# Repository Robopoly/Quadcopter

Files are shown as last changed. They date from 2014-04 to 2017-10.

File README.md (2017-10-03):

# Quadcopter shield

## Introduction
This shield has initially been designed by Robopoly for Aeropoly.
It is made for the [PRismino][prismino], and thus compatible with a Leonardo and most Arduino boards.
It is basically a copy of the nanowii board, except that it is now set as a shield for a Leonardo, rather than a standalone board. The pins are exactly the same.
Therefore, you can use the [Multiwii][multiwii] code, but you will have to make your own configuration.
You can find the Altium and gerber files, as well as the datasheets on this repo.

## Components
The shield has an MPU-9250, a barometer and an attiny4313 that is responsible for the GPS, sonar and optic flow sensor.
The MPU-9250 does not have the same register map as the MPU-9150 previously used if I'm not mistaken. Check that before use.

| chip | purpose | link | Status |
|---|---|---|---|
| MPU-9250 | Accelerometer, gyroscope, magnetometer | [MPU-9250][MPU-9250] | Should work |
| TLV70033DDCR | 3V regulator | [TLV70033DDCR][TLV70033DDCR] | Working |
| PCA9306DP1-G | I2C level translator | [PCA9306DP1-G][PCA9306DP1-G] | Working |
| MS5611 | Barometer | [MS5611] [MS5611] | Should work |
| attiny4313 | Handles optical flow sensor and GPS | [attiny4313][attiny4313] | Not tested |
| hc-05 | Bluetooth | NA | Not working |

Check these against the datasheets. I might have messed up.

| identifier | value |
|---|---|
| R1 -> R5 | 10kOhm |
| R6,8,10 | 1kOhm |
| R7,9 | 2kOhm |
| C5,6,8,9,10  | 0.1uF |
| C7,11 |  10nF |

## Power
You can power the controller through the shield by connecting an 5V BEC to ESC1 pin.
The 3.3V available with the micromatch or double pins are not the ones from the Arduino. Meaning you won't fry your controller if you use too much current.
However, you should stick well within the limits as it powers the MPU-9150 and the I2C level shifter.

## Used pins

### ESC connections
Be careful, only ESC 1 has the ground and 5V pins connected. This is made to avoid ground loops.
The data pin is at the outer side of the board (closest to the pins). The ground pin is the square one.

| ESC  | pin |
|---|---|
| ESC1 | 9 |
| ESC2 |  10 |
| ESC3 | 5 |
| ESC4 | 6 |

### Transmitter connections
Be careful, only THR has the ground and 5V pins connected. This is made to avoid ground loops. If your transmitter does not have a common ground for its channels, you will have to bridge the whole ground line, or mod your receiver.
The data pin is at the outer side of the board (closest to the edge). The ground pin is the square one.

| Command | pin  |
|---|---|
| THR | 7  |
| ROLL | MOSI |
| YAW | SCK  |
| PITCH | MISO |
| AUX1 |  8 |

## Thanks
I'd like to thank the various people that have helped developping this board and namely Felix (aka ronco on multiwii forum), the creator of the Nanowii board.

## Previous version

Previous version (V1, as V2 has never been tested) uses only MPU-9150. The MPU-9150 has the same register map as its brother the MPU-6050 which is used in a Nanowii board. Therefore you can use it as a MPU-6050 if you don't want the magnetometer. This might not be valid for MPU-9250.

| identifier | value |
|---|---|
| R1 -> R5 | 10kOhm |
| C1,2,5,6,7 | 0.1uF |
| C4 |  10nF |
| C3 | 2.2nF |

### MPU-9150
Be careful that the axis for the magnetometer are not the same as for the accelerometer and the gyroscope. The ones on the board are those of the accelerometer.

### Jumper
Either J0 or J1 has to be bridged. If you bridge both, you'll short your power. Never bridge both. These are used to set the address of the MPU-9150.

### ESC connections
Be careful, only ESC 1 has the ground and 5V pins connected. This is made to avoid ground loops.
The data pin is at the outer side of the board (closest to the pins). The ground pin is the square one.

| ESC  | pin |
|---|---|
| ESC1 | 9 |
| ESC2 |  10 |
| ESC3 | 5 |
| ESC4 | 6 |

### Transmitter connections
Be careful, only THR has the ground and 5V pins connected. This is made to avoid ground loops. If your transmitter does not have a common ground for its channels, you will have to bridge the whole ground line, or mod your receiver.
The data pin is at the outer side of the board (closest to the edge). The ground pin is the square one.

| Command | pin  |
|---|---|
| THR | 7  |
| ROLL | MOSI |
| YAW | SCK  |
| PITCH | MISO |
| AUX1 |  8 |

[MS5611]: http://www.te.com/commerce/DocumentDelivery/DDEController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 "MS5611"
[MPU-9250]: http://www.invensense.com/mems/gyro/nineaxis.html "MPU-9250"
[MPU-9150]: http://www.invensense.com/mems/gyro/nineaxis.html "MPU-9150"
[TLV70033DDCR]: http://www.ti.com/product/tlv70033 "TLV70033DDCR"
[atmega32u4]: http://www.atmel.ch/Images/doc7766.pdf "ATmega16U4/32U4 datasheet"
[attiny4313]: http://www.atmel.com/images/doc8246.pdf "attiny4313 datasheet"
[PCA9306DP1-G]: http://www.nxp.com/products/interface_and_connectivity/i2c/i2c_voltage_level_translators/PCA9306DP1.html "PCA9306DP1-G"
[prismino]: https://github.com/Robopoly/PRismino "PRismino"
[multiwii]: http://www.multiwii.com/software "Multiwii"

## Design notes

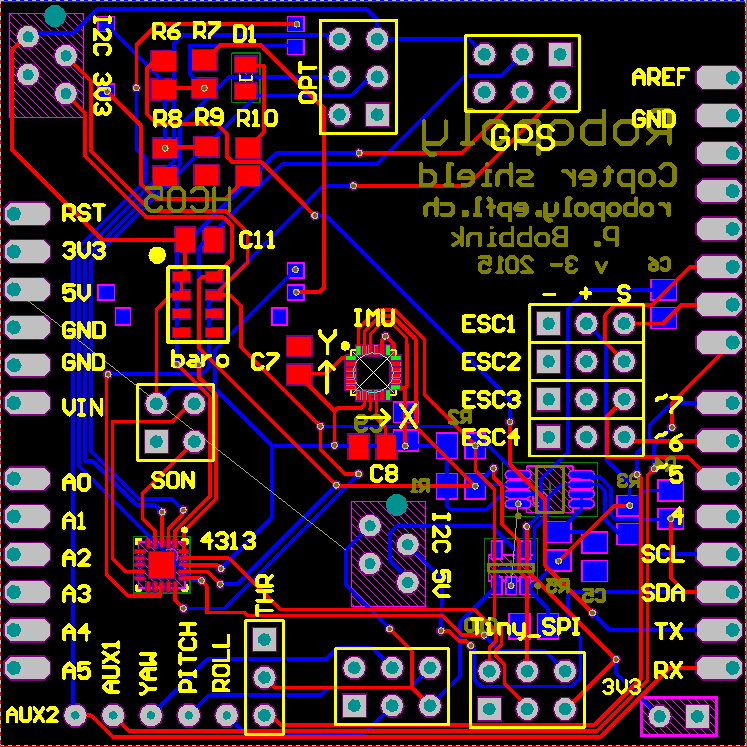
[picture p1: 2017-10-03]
pcb_layout.png

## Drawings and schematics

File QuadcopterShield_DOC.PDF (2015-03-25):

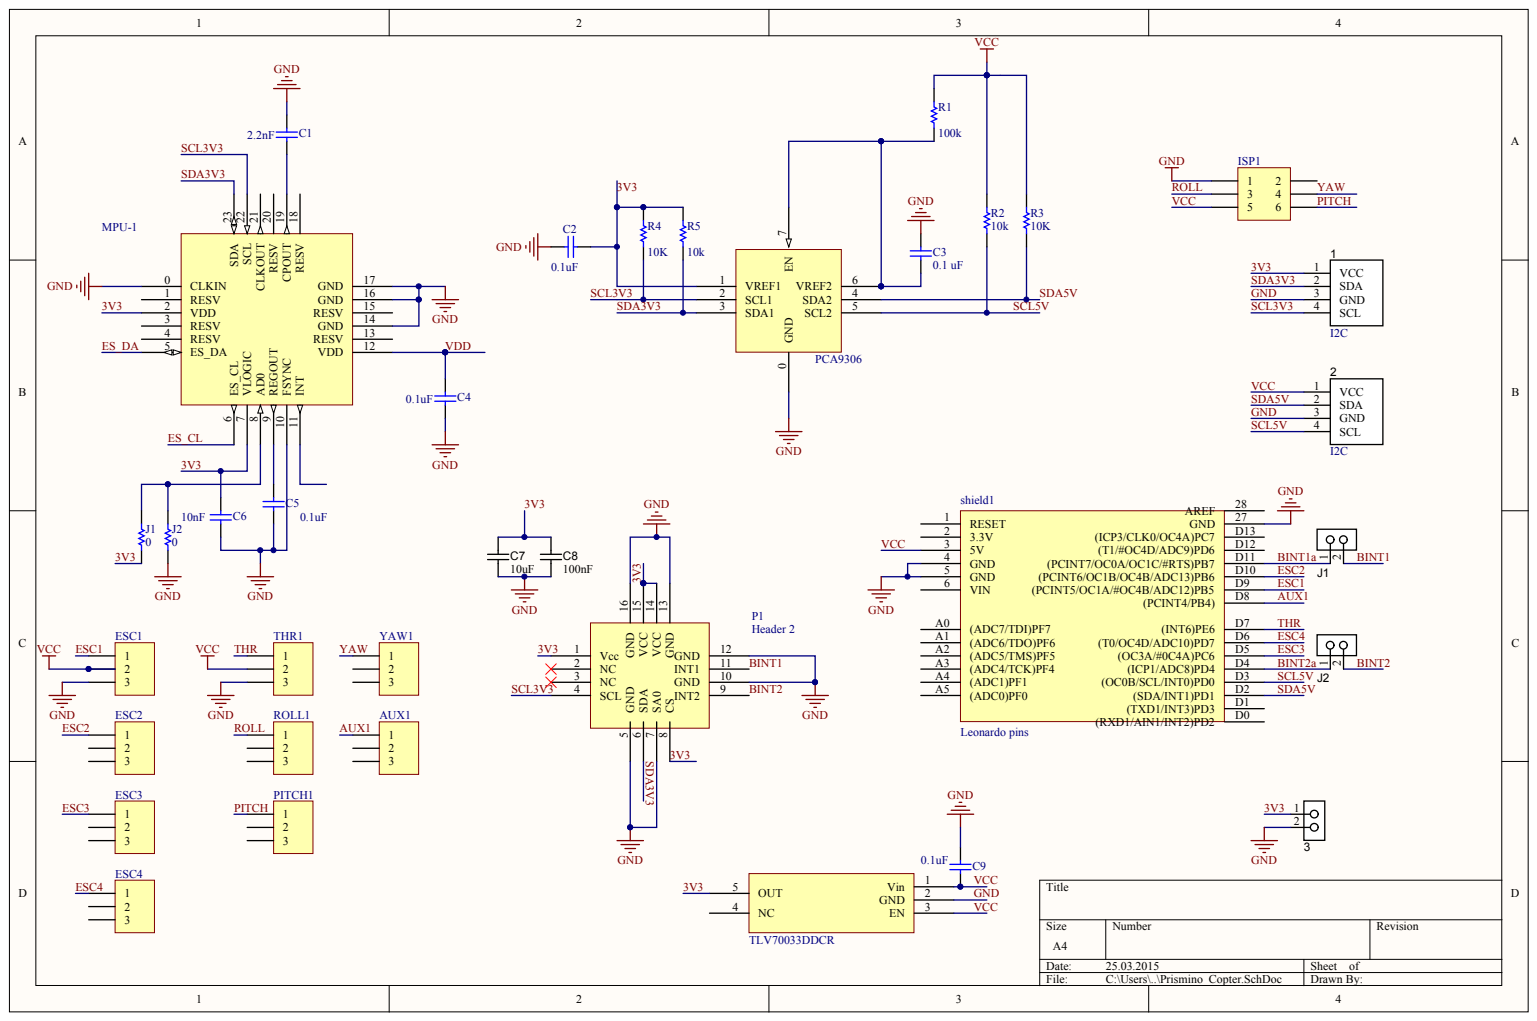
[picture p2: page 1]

RESV 18 CPOUT 19 RESV 20 CLKOUT 21 SCL 22 SDA 23

GND 13 VCC 14 VCC 15 GND 16

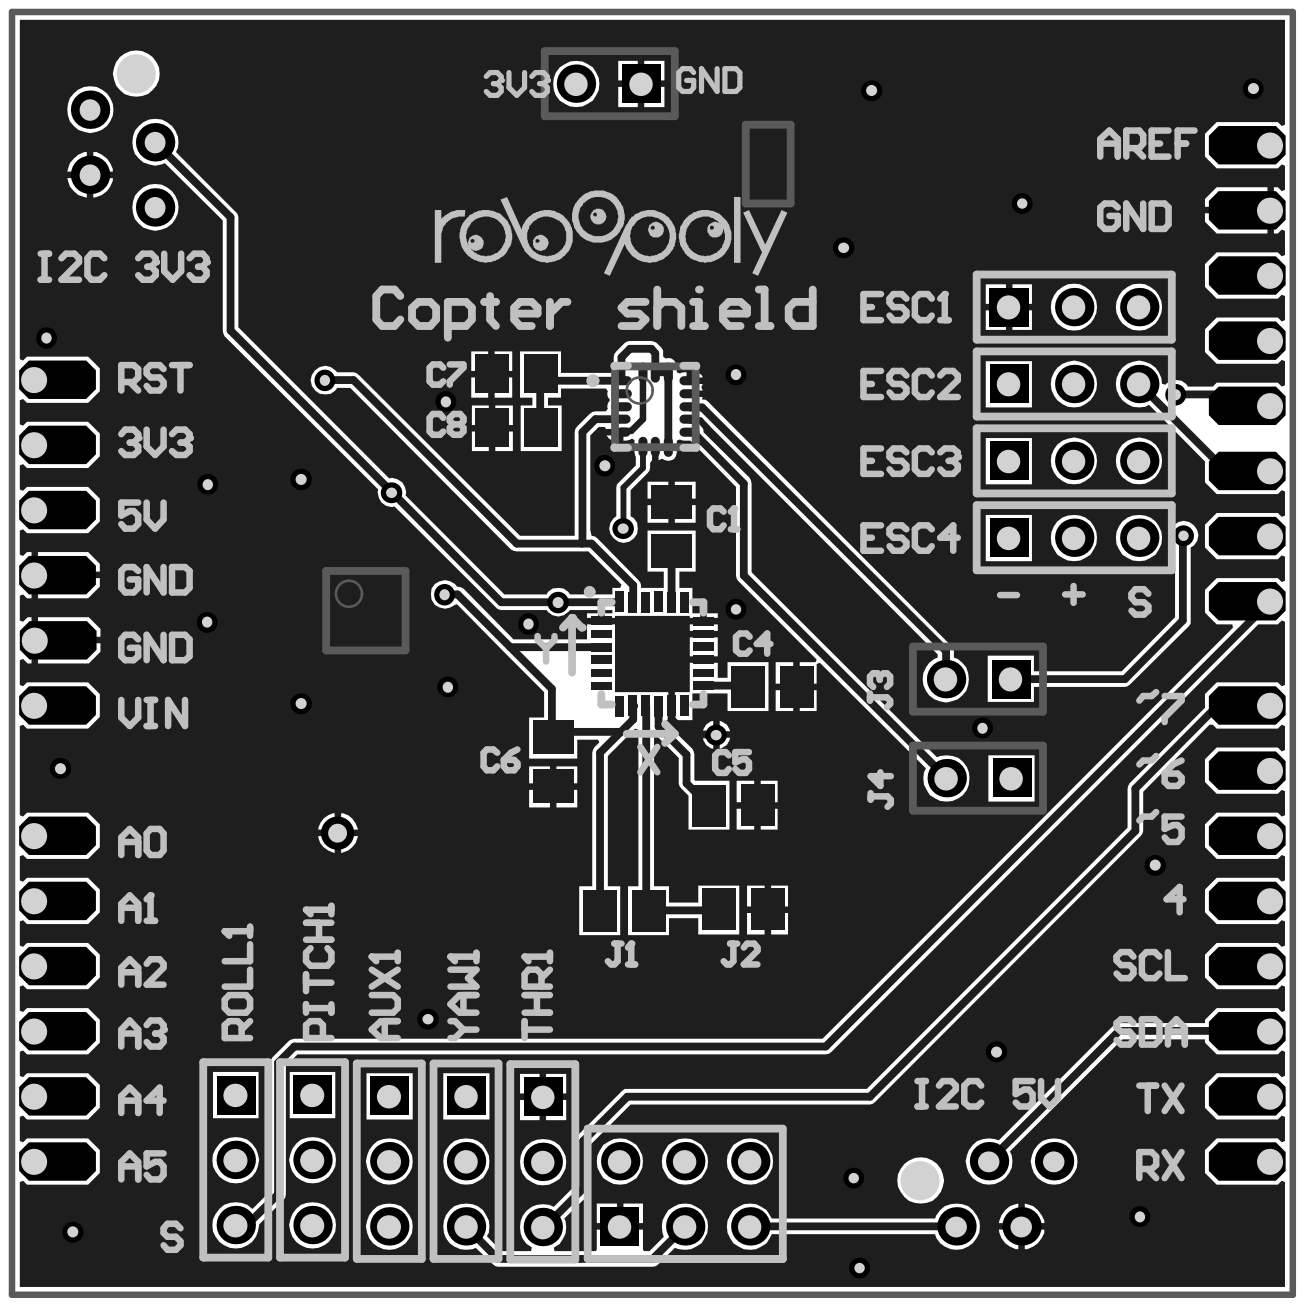
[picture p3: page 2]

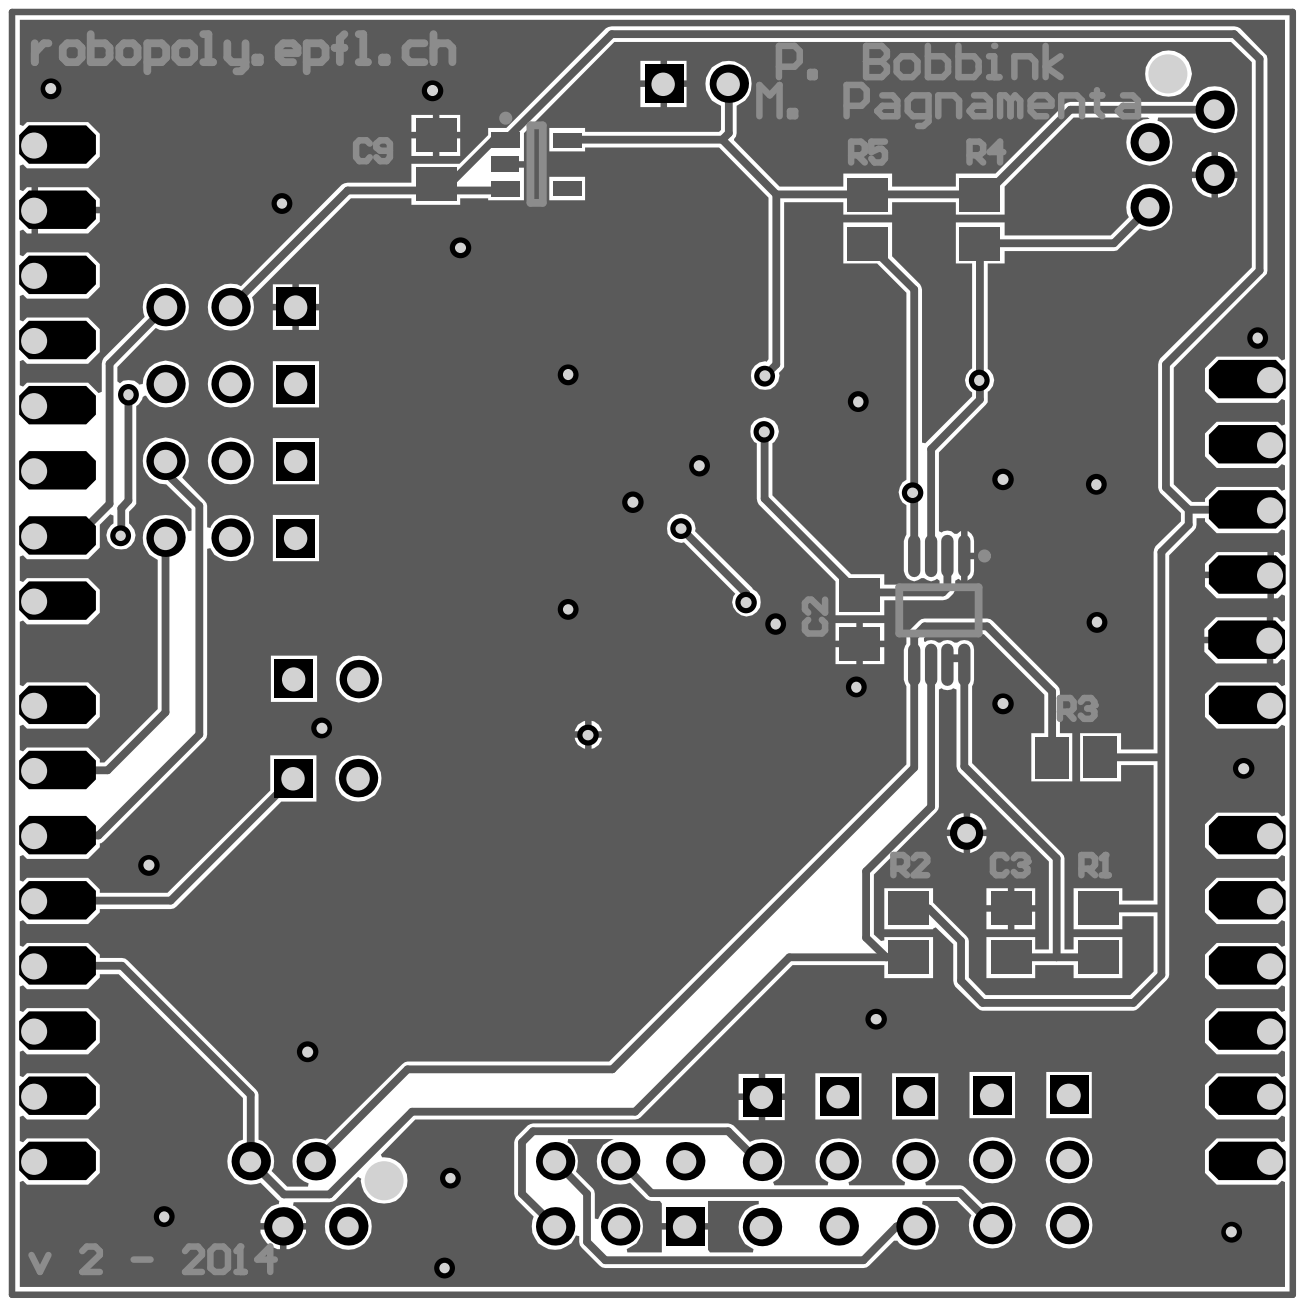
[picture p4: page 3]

Quantit y | Comment | LibRef | Designator | Description | Footprint
2 | I2C | Micromatch-I2C | 1, 2 | Micromatch I2C Connector | TYCO/215079-4
3 | Header 2 | Header 2 | 3, J1, J2 | Header, 2-Pin | HEADER1x2
9 | Header 3 | Header 3 | AUX1, ESC1, ESC2, ESC3, ESC4, PITCH1, ROLL1, THR1, YAW1 | Header, 3-Pin | HDR1X3
7 | C0805 | C0805 | C1, C2, C3, C4, C5, C6, C9 | Ceramic Chip Capacitor -Standard | MELF-R2012-0805
2 | C | C | C7, C8 | Capacitor | C/0805
1 | Header 3X2 | Header 3X2 | ISP1 | Header, 3-Pin, Dual row | HDR2X3
2 | resistor | resistor | J1, J2 | Resistor | MELF-R2012-0805
1 | 9-axis | MPU-9150 | MPU-1 | 9-axis sensor (gyroscope, accelerometre, magnétomètre) | MPU-9150
1 | Header 2 | Barometer LPS331AP | P1 | Header, 2-Pin | HCLGA-16L
1 | PCA9306 | Component_1_1 | PCA1 | I²C shifting voltage | TSOP65P490X110-8N
5 | Res1 | Res1 | R1, R2, R3, R4, R5 | Resistor | MELF-R2012-0805
1 | Leonardo pins | Leonardo pins | shield1 | | Leonardo pins
1 | TLV70033DDCR | TLV700xx | TLV1 | Header, 2-Pin | TLV70033DDCR

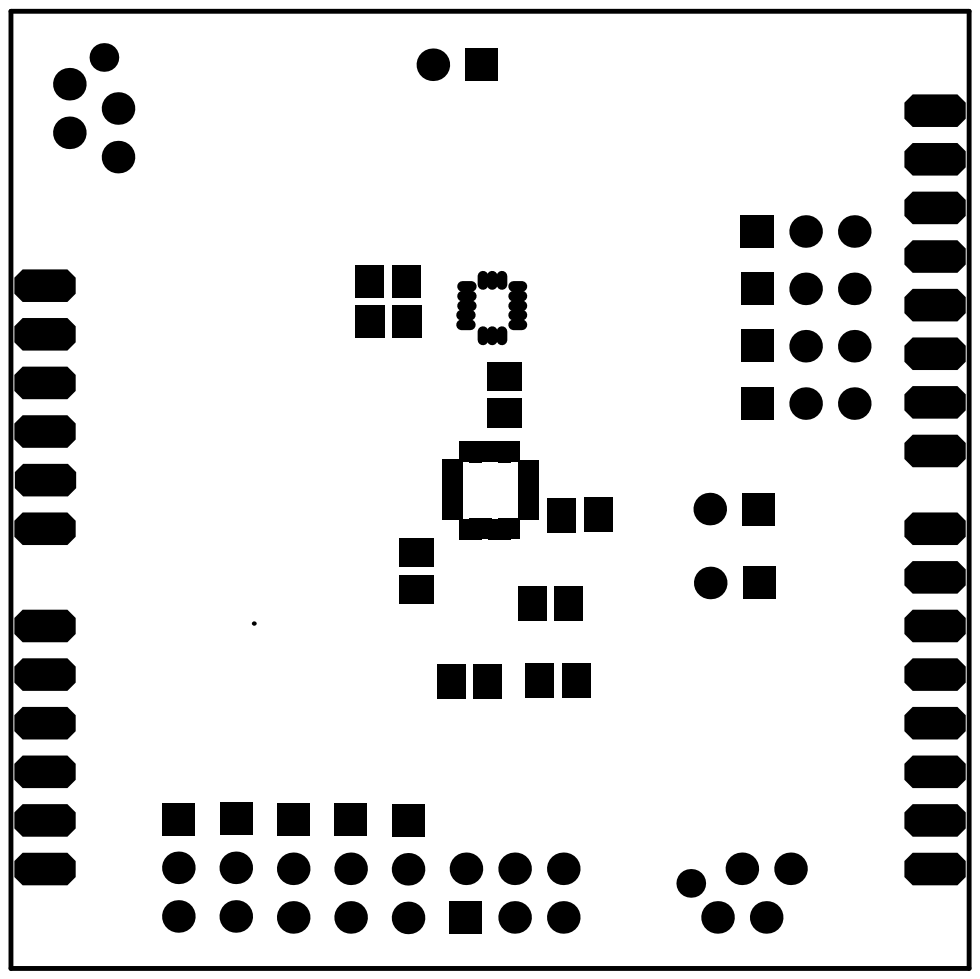
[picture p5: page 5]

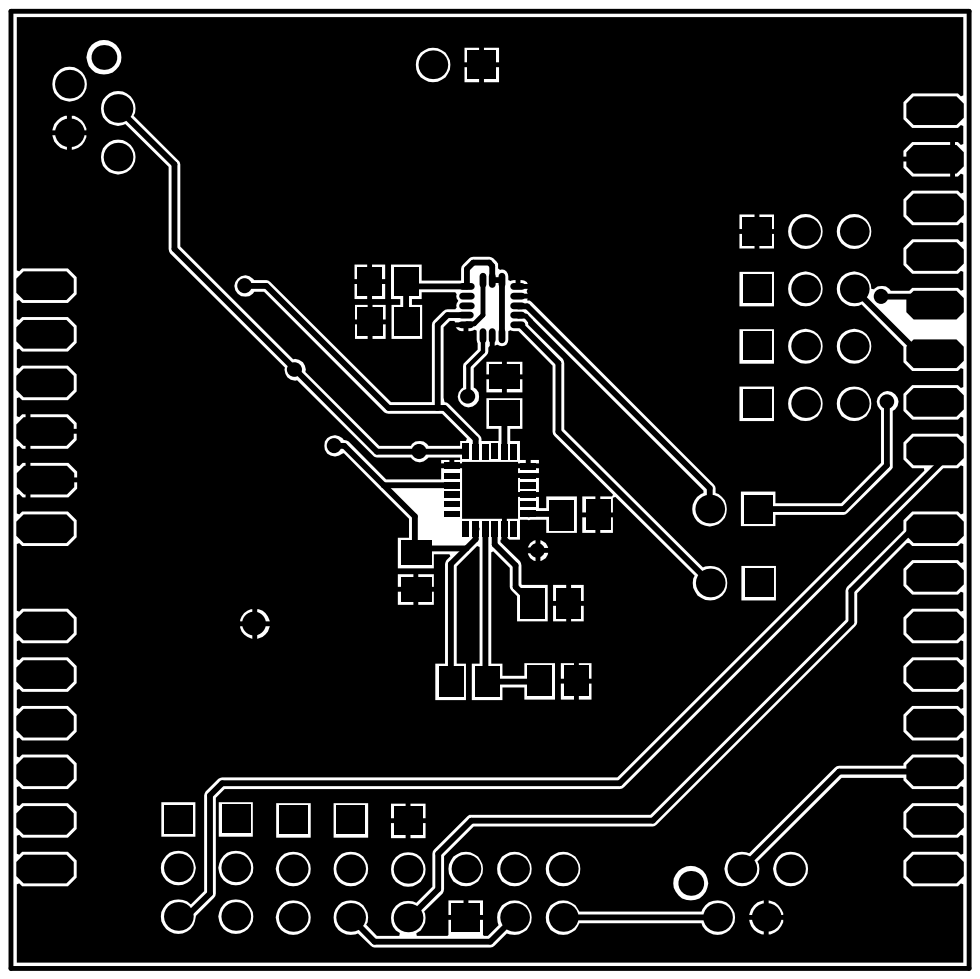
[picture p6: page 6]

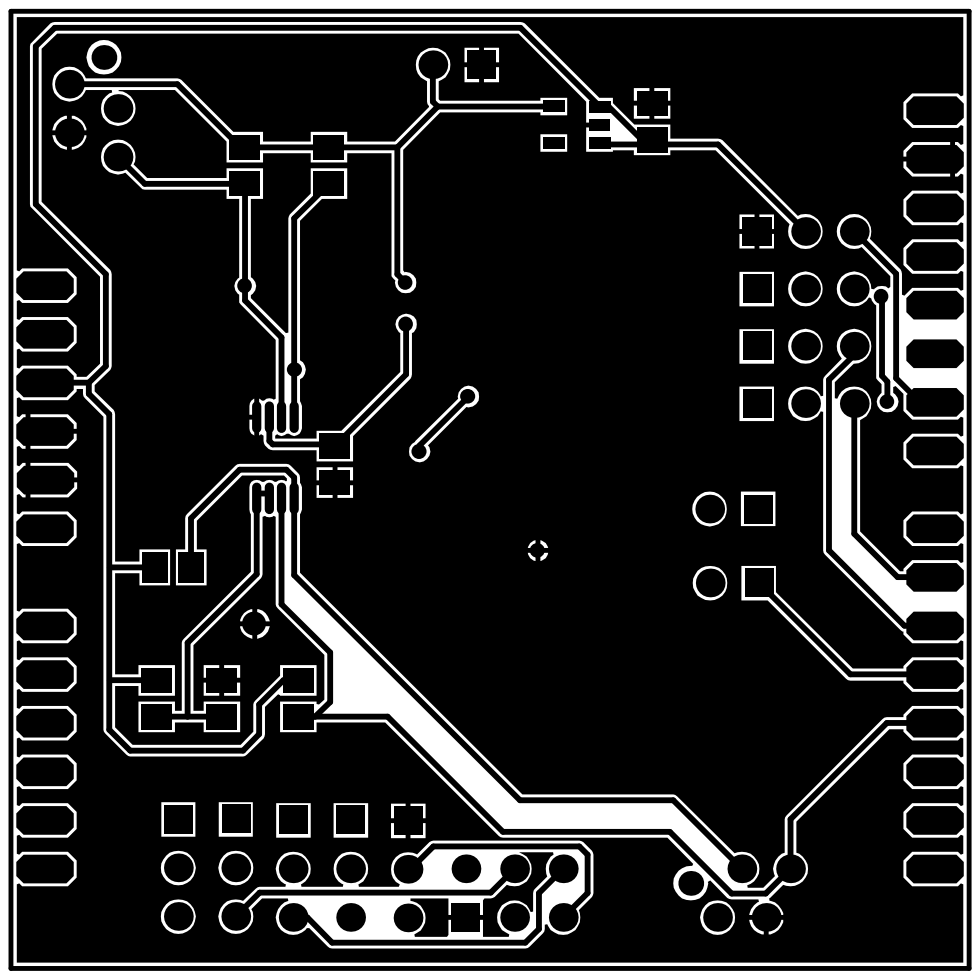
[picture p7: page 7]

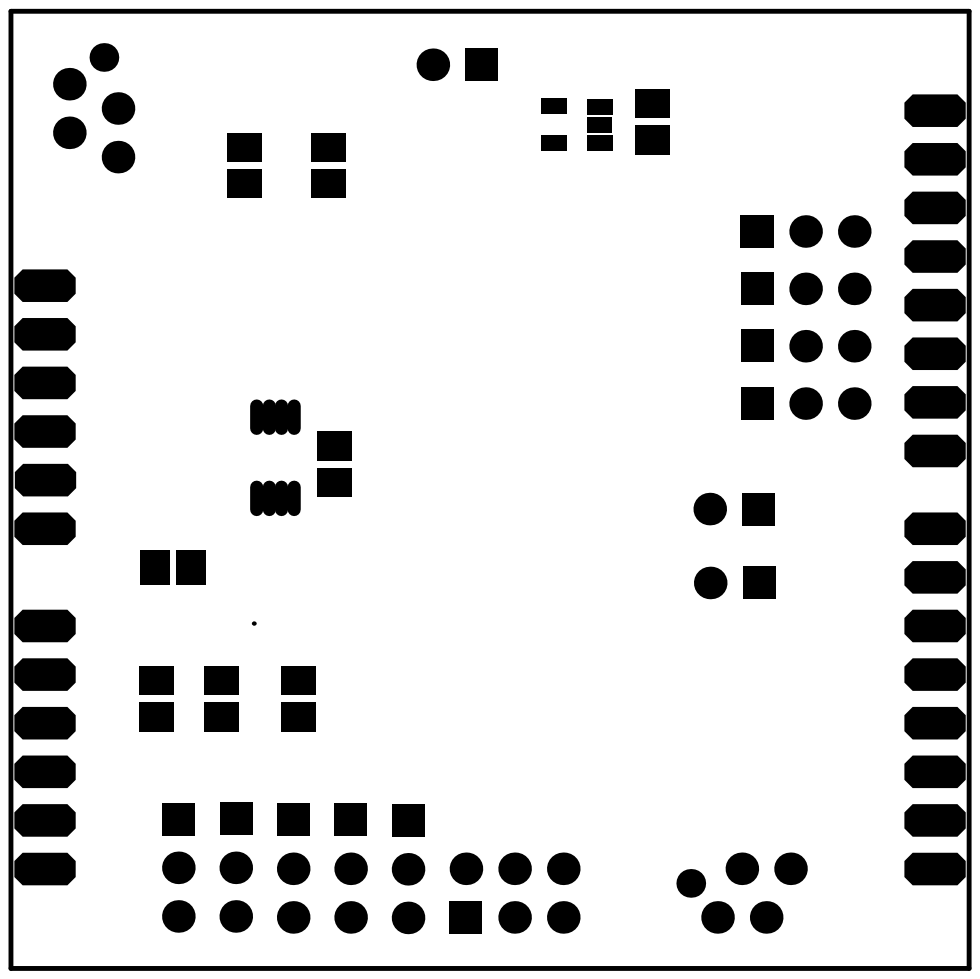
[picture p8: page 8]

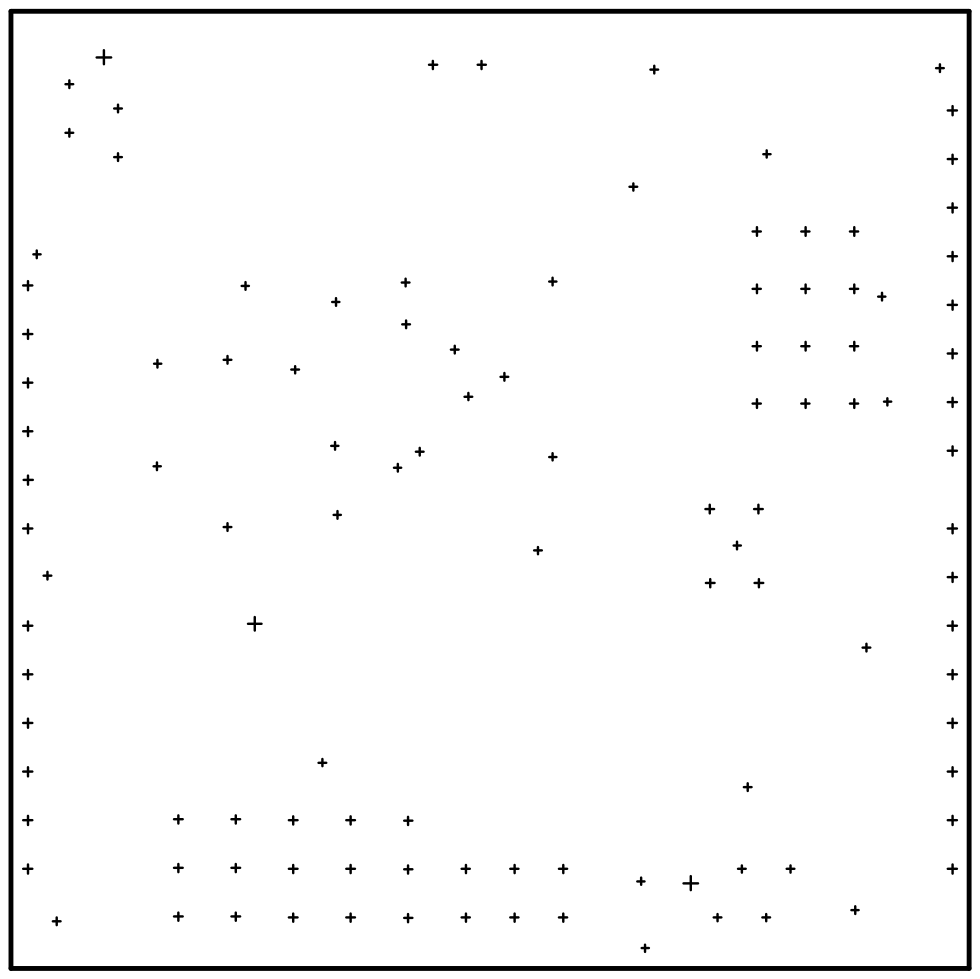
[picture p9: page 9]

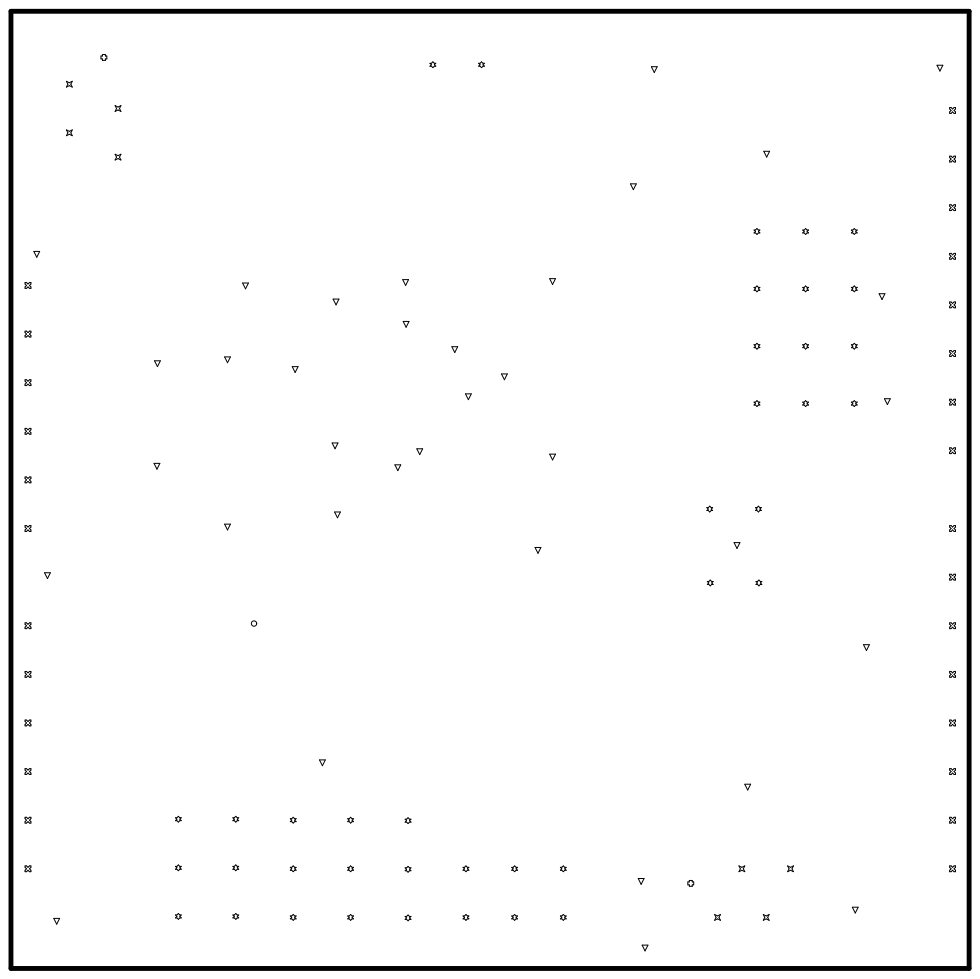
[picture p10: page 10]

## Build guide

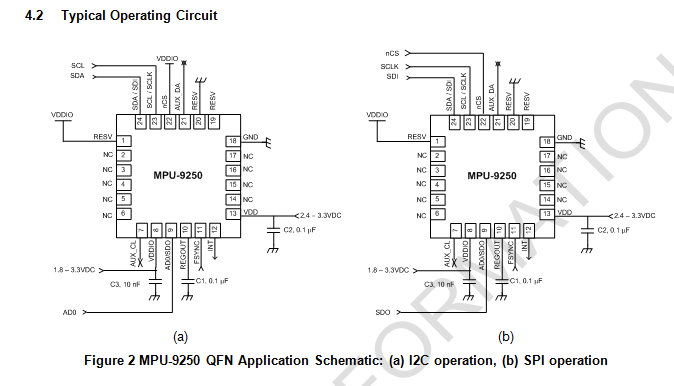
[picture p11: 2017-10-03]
Datasheets/9250 typ operating.PNG

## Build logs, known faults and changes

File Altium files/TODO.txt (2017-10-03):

Pin alignment for RF and ESC (distances)

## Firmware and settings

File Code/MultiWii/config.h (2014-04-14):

#ifndef CONFIG_H_
#define CONFIG_H_

/*************************************************************************************************/
/****           CONFIGURABLE PARAMETERS                                                       ****/
/*************************************************************************************************/

/* this file consists of several sections
 * to create a working combination you must at least make your choices in section 1.
 * 1 - BASIC SETUP - you must select an option in every block.
 *      this assumes you have 4 channels connected to your board with standard ESCs and servos.
 * 2 - COPTER TYPE SPECIFIC OPTIONS - you likely want to check for options for your copter type
 * 3 - RC SYSTEM SETUP
 * 4 - ALTERNATE CPUs & BOARDS - if you have
 * 5 - ALTERNATE SETUP - select alternate RX (SBUS, PPM, etc.), alternate ESC-range, etc. here
 * 6 - OPTIONAL FEATURES - enable nice to have features here (FlightModes, LCD, telemetry, battery monitor etc.)
 * 7 - TUNING & DEVELOPER - if you know what you are doing; you have been warned
 *     - (ESCs calibration, Dynamic Motor/Prop Balancing, Diagnostics,Memory savings.....)
 * 8 - DEPRECATED - these features will be removed in some future release
 */

/* Notes:
 * 1. parameters marked with (*) in the comment are stored in eeprom and can be changed via serial monitor or LCD.
 * 2. parameters marked with (**) in the comment are stored in eeprom and can be changed via the GUI
 */


/*************************************************************************************************/
/*****************                                                                 ***************/
/****************  SECTION  1 - BASIC SETUP                                                *******/
/*****************                                                                 ***************/
/*************************************************************************************************/

  /**************************    The type of multicopter    ****************************/
    //#define GIMBAL
    //#define BI
    //#define TRI
    #define QUADP
    //#define QUADX
    //#define Y4
    //#define Y6
    //#define HEX6
    //#define HEX6X
    //#define HEX6H  // New Model
    //#define OCTOX8
    //#define OCTOFLATP
    //#define OCTOFLATX
    //#define FLYING_WING
    //#define VTAIL4
    //#define AIRPLANE
    //#define SINGLECOPTER
    //#define DUALCOPTER
    //#define HELI_120_CCPM
    //#define HELI_90_DEG

  /****************************    Motor minthrottle    *******************************/
    /* Set the minimum throttle command sent to the ESC (Electronic Speed Controller)
       This is the minimum value that allow motors to run at a idle speed  */
    //#define MINTHROTTLE 1300 // for Turnigy Plush ESCs 10A
    //#define MINTHROTTLE 1120 // for Super Simple ESCs 10A
    //#define MINTHROTTLE 1064 // special ESC (simonk)
    //#define MINTHROTTLE 1050 // for brushed ESCs like ladybird
    #define MINTHROTTLE 1150 // (*) (**)

  /****************************    Motor maxthrottle    *******************************/
    /* this is the maximum value for the ESCs at full power, this value can be increased up to 2000 */
    #define MAXTHROTTLE 1850

  /****************************    Mincommand          *******************************/
    /* this is the value for the ESCs when they are not armed
       in some cases, this value must be lowered down to 900 for some specific ESCs, otherwise they failed to initiate */
    #define MINCOMMAND  1000

  /**********************************    I2C speed   ************************************/
    #define I2C_SPEED 100000L     //100kHz normal mode, this value must be used for a genuine WMP
    //#define I2C_SPEED 400000L   //400kHz fast mode, it works only with some WMP clones

  /***************************    Internal i2c Pullups   ********************************/
    /* enable internal I2C pull ups (in most cases it is better to use external pullups) */
    //#define INTERNAL_I2C_PULLUPS

  /**************************************************************************************/
  /*****************          boards and sensor definitions            ******************/
  /**************************************************************************************/
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

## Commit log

2014-03-25 documentation update
    Added values for capacitors and resistors. Minor fixes in the text.
2014-04-14 Added code
    [config.h]
2014-07-15 documentation update
    [Bill of Materials-Prismino_Copter.xls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]
2015-03-25 New sources and doc
    Minor corrections in the PCB
    [Prismino_Copter.GBL, Prismino_Copter.GBO, Prismino_Copter.GBS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]
2017-10-03 V3
    Added pcb libraries as well
    [GPS.PcbLib, GPS.SchLib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]
2017-10-03 Wrong files
    Had the wrong files, should be fixed. Updated doc
    [Bill of Materials-Prismino_Copter.xls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]
